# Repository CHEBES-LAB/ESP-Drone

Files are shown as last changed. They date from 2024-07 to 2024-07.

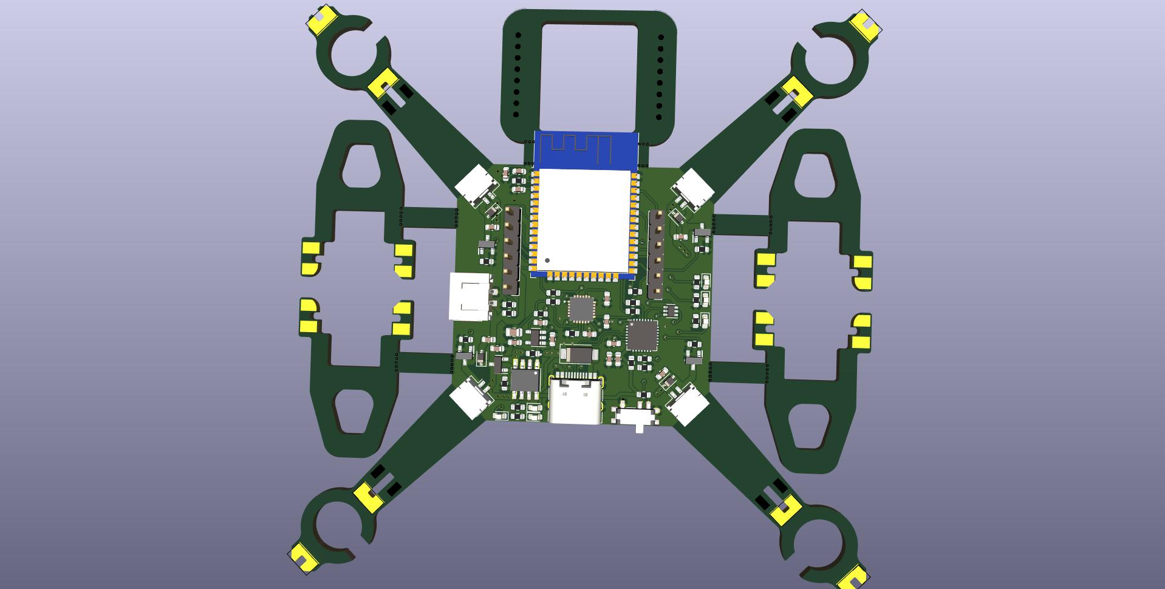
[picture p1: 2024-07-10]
Hardware/PDF/ESP32 drone.jpg

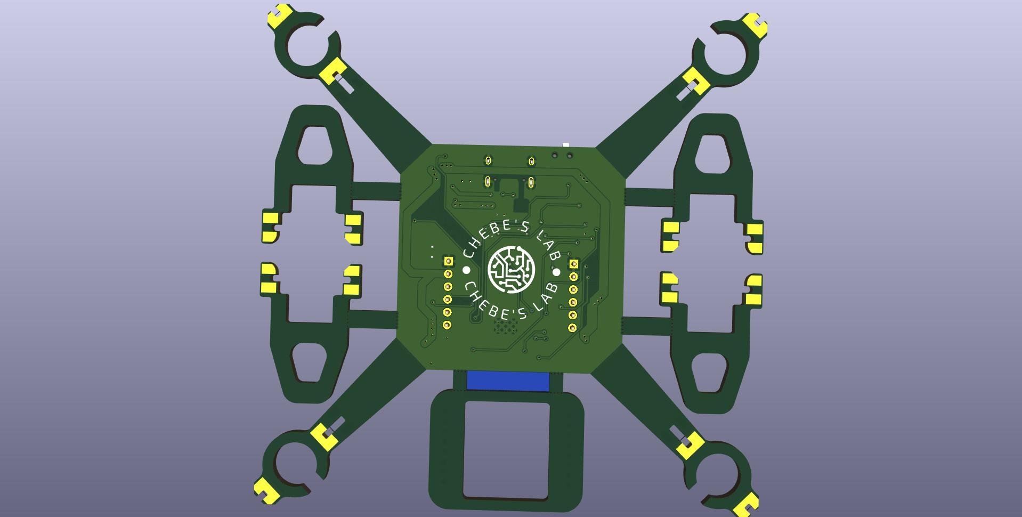
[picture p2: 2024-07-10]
Hardware/PDF/ESP32 drone back.jpg

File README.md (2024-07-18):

# ESP-Drone

image_tooltip

<br>

<br>

For a full tutorial check out our [ESP32 Drone Article](https://circuitdigest.com/microcontroller-projects/DIY-wifi-controlled-drone).
For working video:  [How to build an ESP32 Drone](https://youtu.be/uzZjk0TQKtU).

Drones have rapidly evolved from niche hobbies to versatile tools with a wide range of applications, from photography to agriculture or even for defense and military purposes. Depending on the application, features and payload capacity their price will vary from pocket changes to a few million. Even though the basic principle behind these drones may appear simple, there is a lot of technology and computation that goes behind it for proper operations and a desired result from these drones. For example, maintaining stability while in the air requires precision sensors such as a Gyroscope and proper processing of reading taken with it. In this project we are going to make such a drone which can be easily controlled using our phones.
This DIY drone is small in size and can be built using easily available components such as ESP32 modules, MPU6050 IMU, coreless motors and plastic propellers.
<br>For anyone who is trying to flash the firmware using ESP32 Flash Download Tool, here are the file offsets for each binary
<br>0x1000 bootloader.bin
<br>0x10000 ESPDrone.bin
<br>0x8000 partition-table.bin
<br>
[Note: As this projects are very simple we are only providing the code, schemaitic, and a few essential images if you want to get the images or code explanations do check out the Circuit Digest website.
<br>
<br>

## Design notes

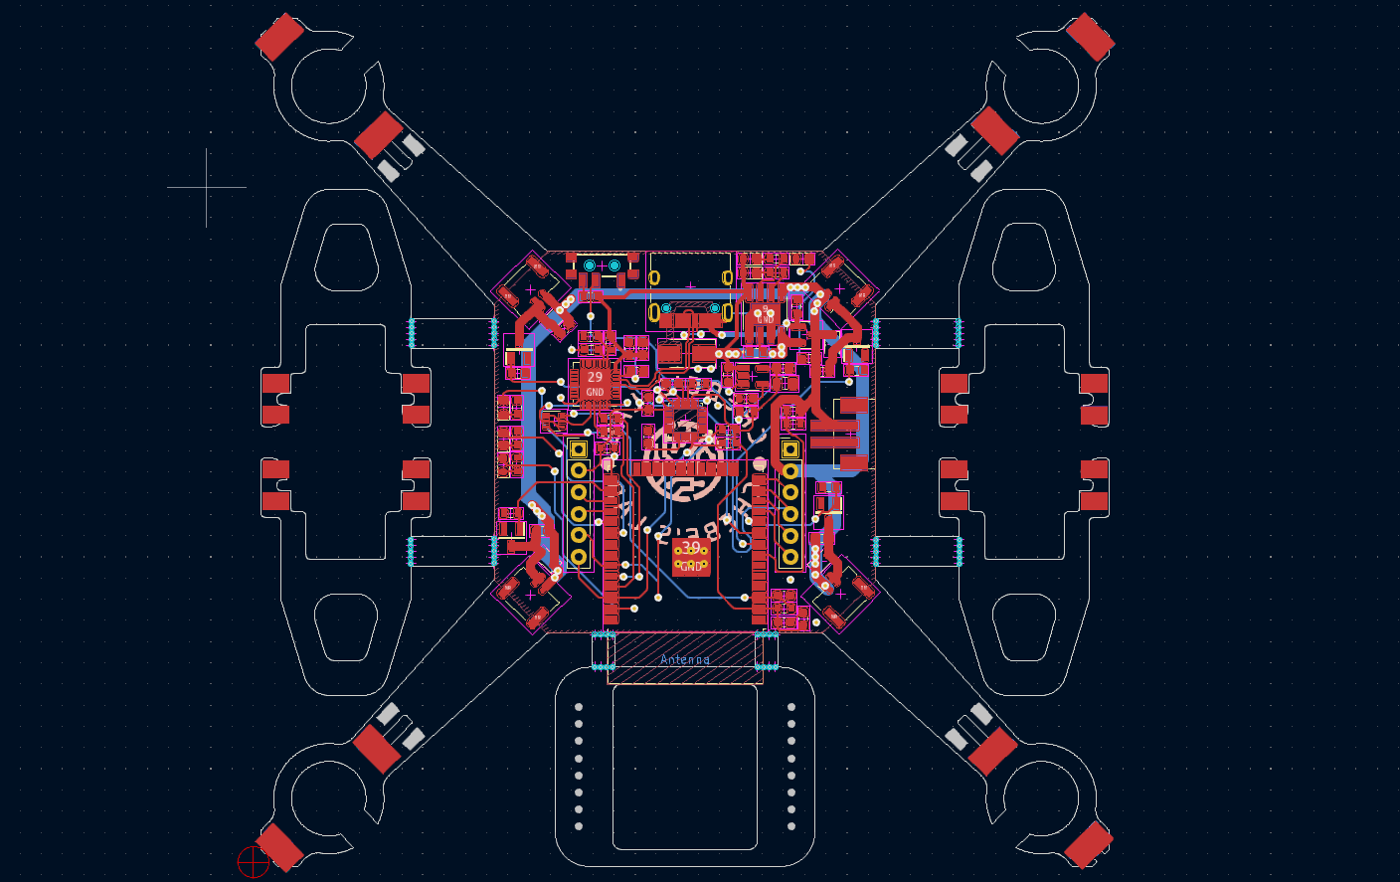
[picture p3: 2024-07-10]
Hardware/PDF/PCB .png

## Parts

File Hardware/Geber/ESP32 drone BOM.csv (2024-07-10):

Reference | Value | Datasheet | Footprint | Qty | DNP
C1,C4 | 10u | ~ | Capacitor_SMD:C_0603_1608Metric | 2
C2 | 470pF | ~ | Capacitor_SMD:C_0603_1608Metric | 1
C3 | 2.2uF | ~ | Capacitor_SMD:C_0805_2012Metric | 1
C5 | 10uF | ~ | Capacitor_SMD:C_0603_1608Metric | 1
C6,C11,C12,C13 | 0.1uf | ~ | Capacitor_SMD:C_0603_1608Metric | 4
C7,C9,C14 | 10uf | ~ | Capacitor_SMD:C_0603_1608Metric | 3
C8,C10,C15,C16,C17,C18 | 1uf | ~ | Capacitor_SMD:C_0603_1608Metric | 6
D1 | SS34 | https://www.diodes.com/assets/Datasheets/ds16008.pdf | Diode_SMD:D_SMA | 1
D2,D3,D4,D5 | 1N4148W | https://www.vishay.com/docs/85748/1n4148w.pdf | Diode_SMD:D_SOD-323 | 4
IC1 | TP4056 |  | AddedLibraries:SOP127P600X175-9N | 1
J1 | USB_C_Receptacle_USB2.0 | https://www.usb.org/sites/default/files/documents/usb_type-c.zip | Connector_USB:USB_C_Receptacle_HRO_TYPE-C-31-M-12 | 1
J2,J4,J5,J6 | Conn_01x02_Female | ~ | Connector_JST:JST_GH_SM02B-GHS-TB_1x02-1MP_P1.25mm_Horizontal | 4
J3 | B2B-PH-SM4-TB_LF__SN_ |  | AddedLibraries:SM4-CON | 1
J8,J9 | Conn_01x06_Female | ~ | Connector_PinHeader_2.54mm:PinHeader_1x06_P2.54mm_Vertical | 2
LED1 | POW_LED | ~ | LED_SMD:LED_0603_1608Metric | 1
LED2,LED3 | CHG | ~ | LED_SMD:LED_0603_1608Metric | 2
LED4,LED5,LED6 | LED | ~ | LED_SMD:LED_0603_1608Metric | 3
R1 | 470R | ~ | Resistor_SMD:R_0603_1608Metric | 1
R2,U1,U4,U5 | 100K | ~ | Resistor_SMD:R_0603_1608Metric | 4
R3,R4 | 1.3K | ~ | Resistor_SMD:R_0603_1608Metric | 2
R5 | 47.5k | ~ | Resistor_SMD:R_0603_1608Metric | 1
R6 | 22.1k | ~ | Resistor_SMD:R_0603_1608Metric | 1
R7,R10,R11,R12,R14,R18,R19,R20,R21 | 10k | ~ | Resistor_SMD:R_0603_1608Metric | 9
R8,R9 | 1k | ~ | Resistor_SMD:R_0603_1608Metric | 2
R13 | 4.7k | ~ | Resistor_SMD:R_0603_1608Metric | 1
R15,R16,R17 | 1K | ~ | Resistor_SMD:R_0603_1608Metric | 3
Rprog1 | 3.3K | ~ | Resistor_SMD:R_0603_1608Metric | 1
SW1 | CUS-12TB |  | AddedLibraries:CUS-12B | 1
T1,T2,T3,T4 | SI2302DS-T1 | https://4donline.ihs.com/images/VipMasterIC/IC/SILX/SILXS08192/SILXS08192-1.pdf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 | AddedLibraries:SOT95P237X112-3N | 4
U2 | AO3401 | ~ | Package_TO_SOT_SMD:SOT-23 | 1
U3 | MIC5219-3.3YM5 | http://ww1.microchip.com/downloads/en/DeviceDoc/MIC5219-500mA-Peak-Output-LDO-Regulator-DS20006021A.pdf | Package_TO_SOT_SMD:SOT-23-5 | 1
U6 | CP2102N-Axx-xQFN28 | https://www.silabs.com/documents/public/data-sheets/cp2102n-datasheet.pdf | Package_DFN_QFN:QFN-28-1EP_5x5mm_P0.5mm_EP3.35x3.35mm | 1
U7 | DDC114TU-7-F |  | Package_TO_SOT_SMD:SOT-363_SC-70-6 | 1
U8 | ESP32-WROOM-32 | https://www.espressif.com/sites/default/files/documentation/esp32-wroom-32_datasheet_en.pdf | RF_Module:ESP32-WROOM-32 | 1
U9 | MPU-6050 |  | AddedLibraries:QFN50P400X400X95-24N | 1

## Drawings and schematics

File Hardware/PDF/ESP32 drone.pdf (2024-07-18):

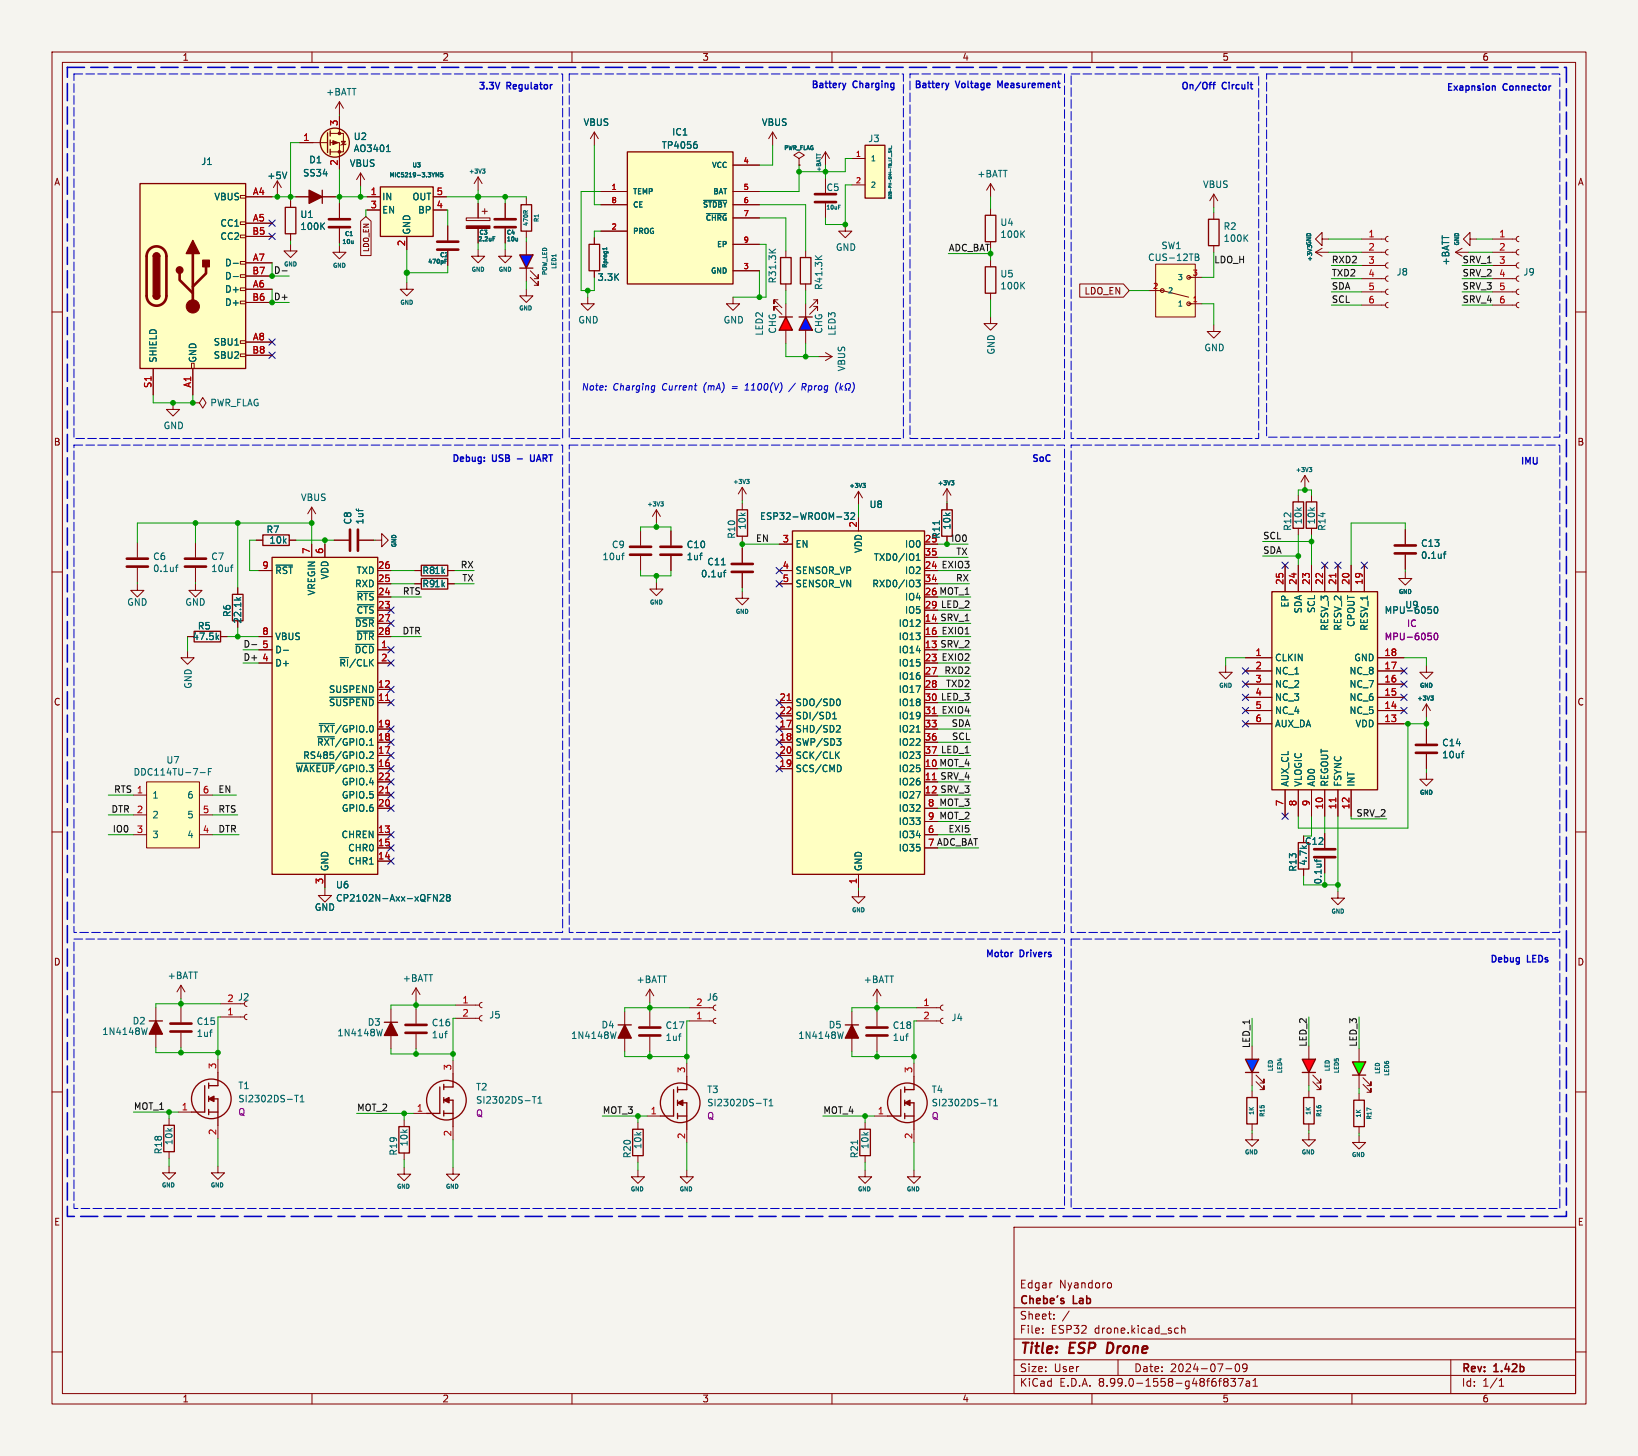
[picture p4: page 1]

Battery Voltage Measurement SoC

9 RESV_3 22 REGOUT 10 RESV_2 21 FSYNC 11 CPOUT 20 INT 12 RESV_1 19 GND 18 NC_8 17 NC_7 16 NC_6 15 NC_5 14 VDD 13 C12 0.1uf R134.7k U8 ESP32-WROOM-32 EN 3 SENSOR_VP 4 SENSOR_VN 5 SDO/SD0 21 SDI/SD1 22 SHD/SD2 17 SWP/SD3 18 SCK/CLK 20 SCS/CMD 19 VDD

3 TXD 26 RXD 25 ~{RTS} 24 ~{CTS} 23 ~{DSR} 27 ~{DTR} 28 ~{DCD}1 ~{RI}/CLK2 SUSPEND 12 ~{SUSPEND}11 ~{TXT}/GPIO.019 ~{RXT}/GPIO.118 RS485/GPIO.2 17 ~{WAKEUP}/GPIO.316 GPIO.4 22 GPIO.5 21 GPIO.6 20 CHREN 13 CHR0 15 CHR1 14 R7
4 U7 DDC114TU-7-F GND

3 TXD 26 RXD 25 ~{RTS} 24 ~{CTS} 23 ~{DSR} 27 ~{DTR} 28 ~{DCD}1 ~{RI}/CLK2 SUSPEND 12 ~{SUSPEND}11 ~{TXT}/GPIO.019 ~{RXT}/GPIO.118 RS485/GPIO.2 17 ~{WAKEUP}/GPIO.316 GPIO.4 22 GPIO.5 21 GPIO.6 20 CHREN 13 CHR0 15 CHR1 14 U6 CP2102N-Axx-xQFN28 GND

9 RESV_3 22 REGOUT 10 RESV_2 21 FSYNC 11 CPOUT 20 INT 12 RESV_1 19 GND 18 NC_8 17 NC_7 16 NC_6 15 NC_5 14 VDD 13 U9 MPU-6050

Id: 1/1 Title: ESP Drone

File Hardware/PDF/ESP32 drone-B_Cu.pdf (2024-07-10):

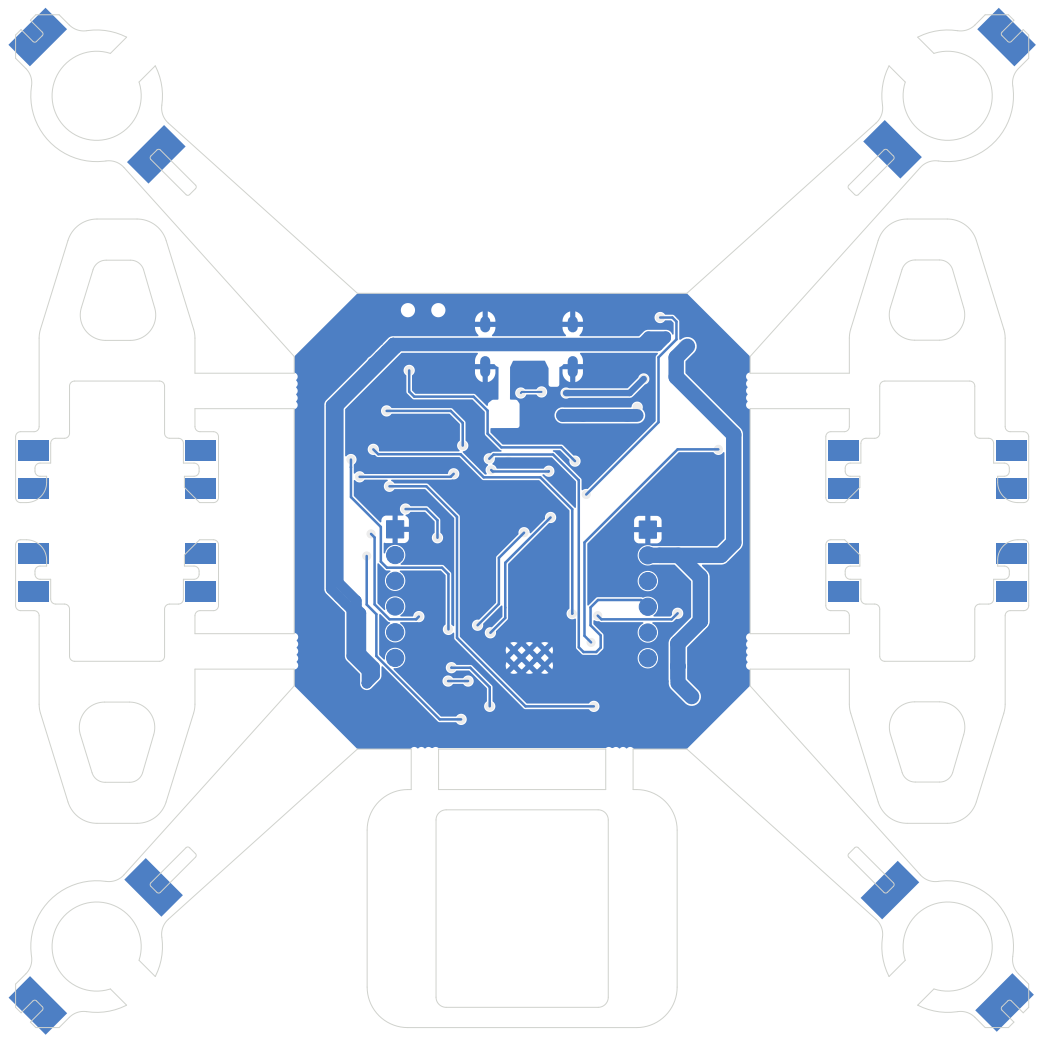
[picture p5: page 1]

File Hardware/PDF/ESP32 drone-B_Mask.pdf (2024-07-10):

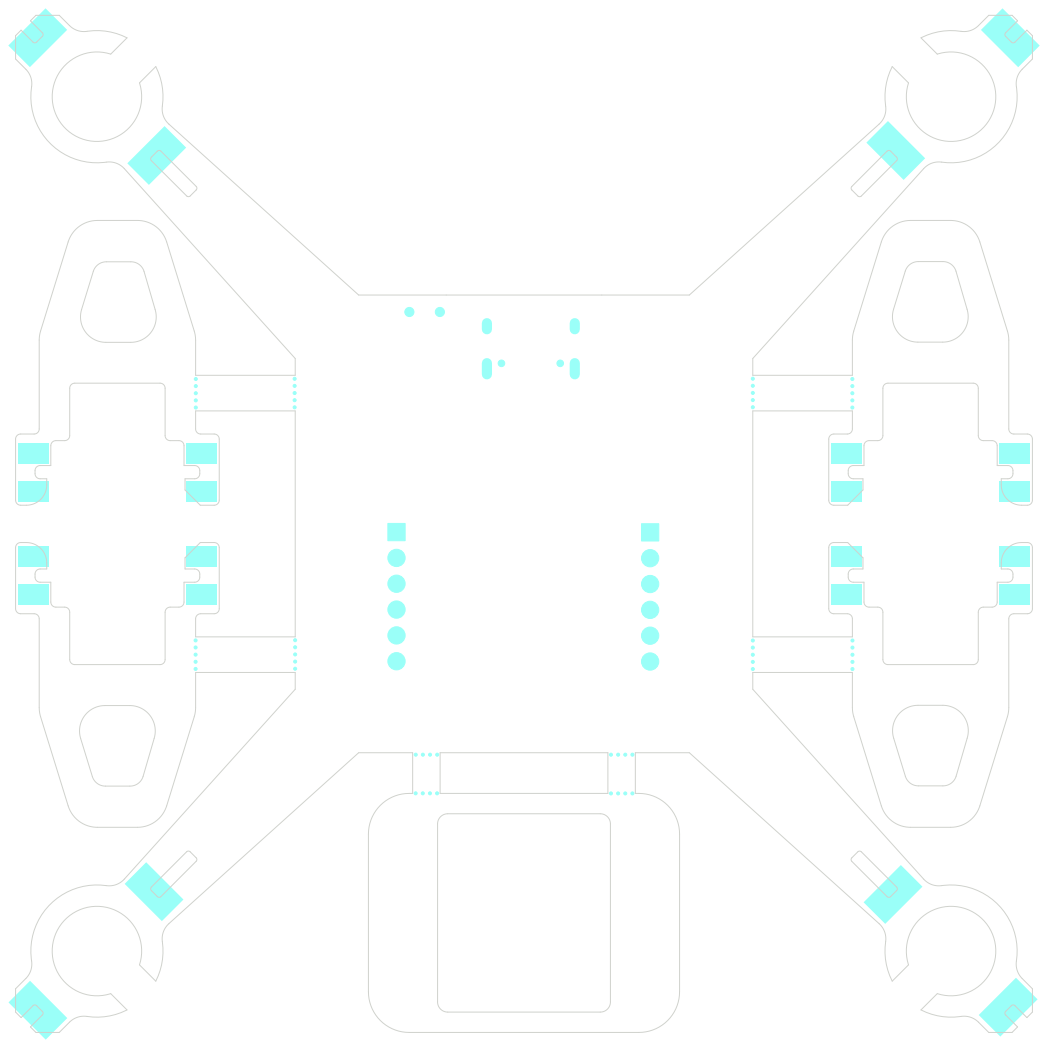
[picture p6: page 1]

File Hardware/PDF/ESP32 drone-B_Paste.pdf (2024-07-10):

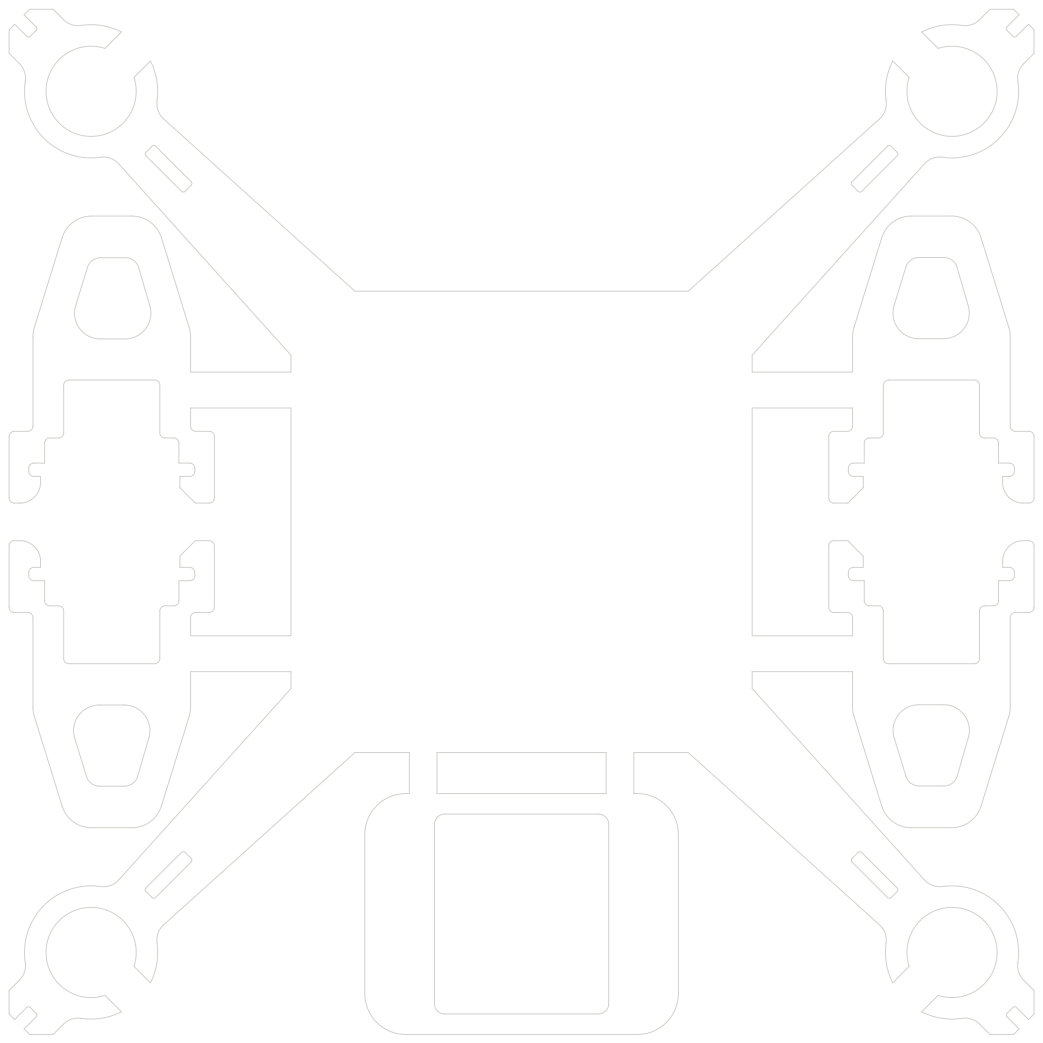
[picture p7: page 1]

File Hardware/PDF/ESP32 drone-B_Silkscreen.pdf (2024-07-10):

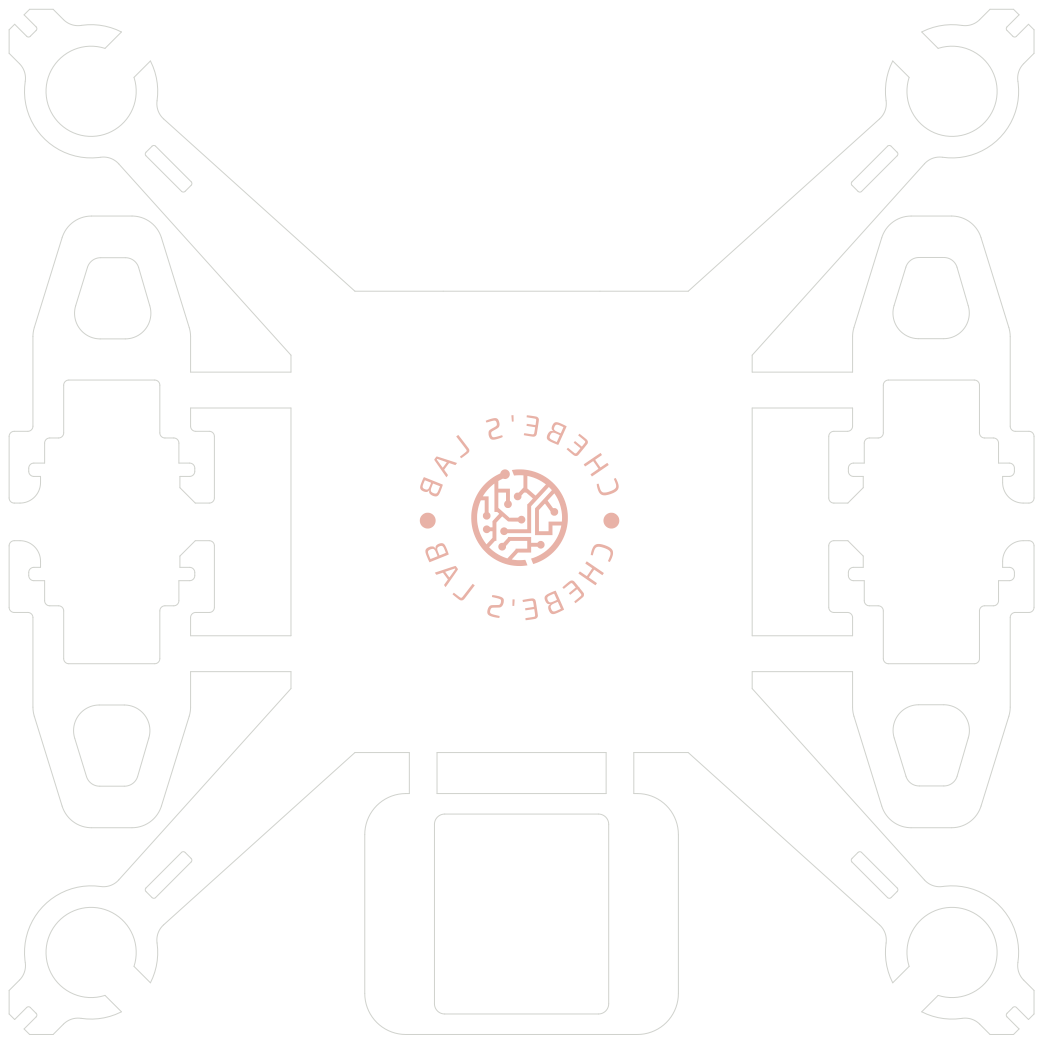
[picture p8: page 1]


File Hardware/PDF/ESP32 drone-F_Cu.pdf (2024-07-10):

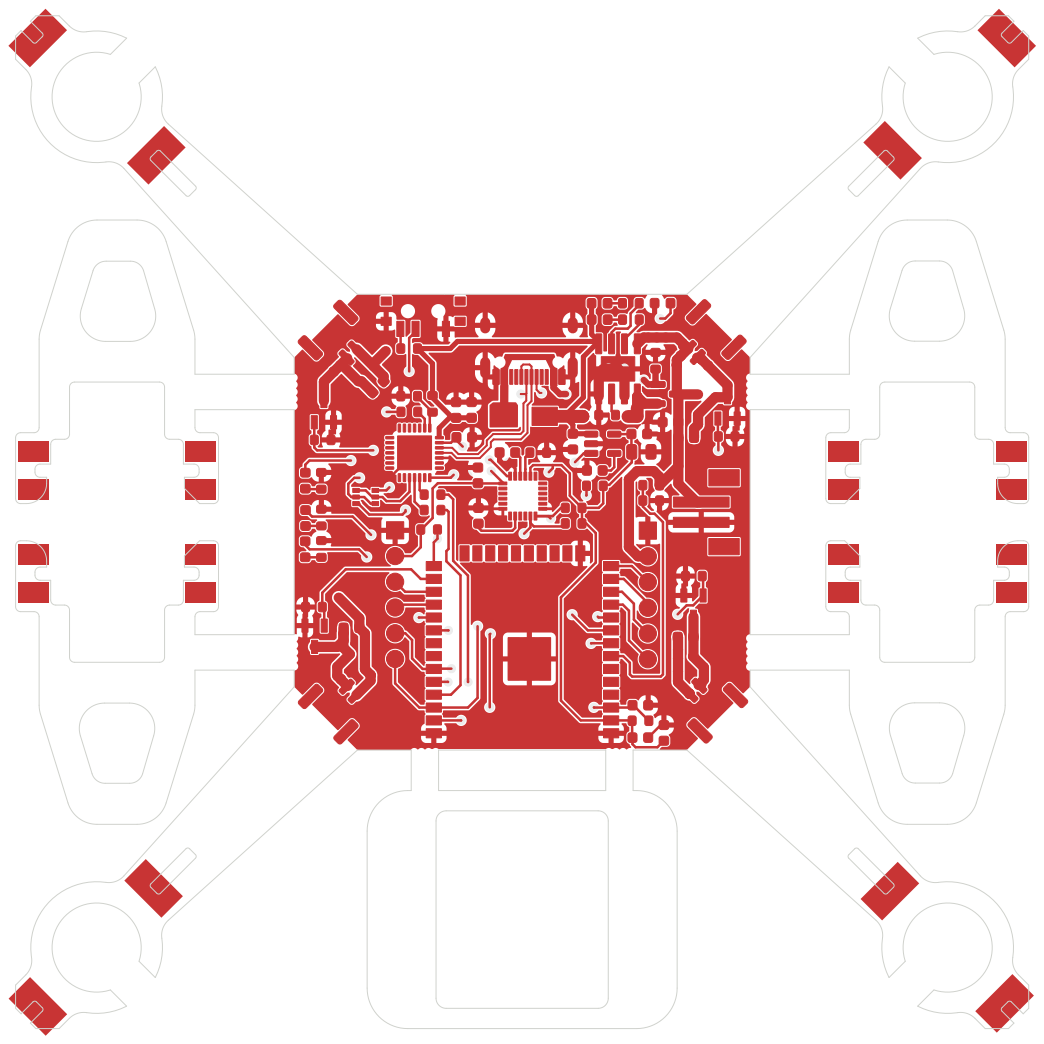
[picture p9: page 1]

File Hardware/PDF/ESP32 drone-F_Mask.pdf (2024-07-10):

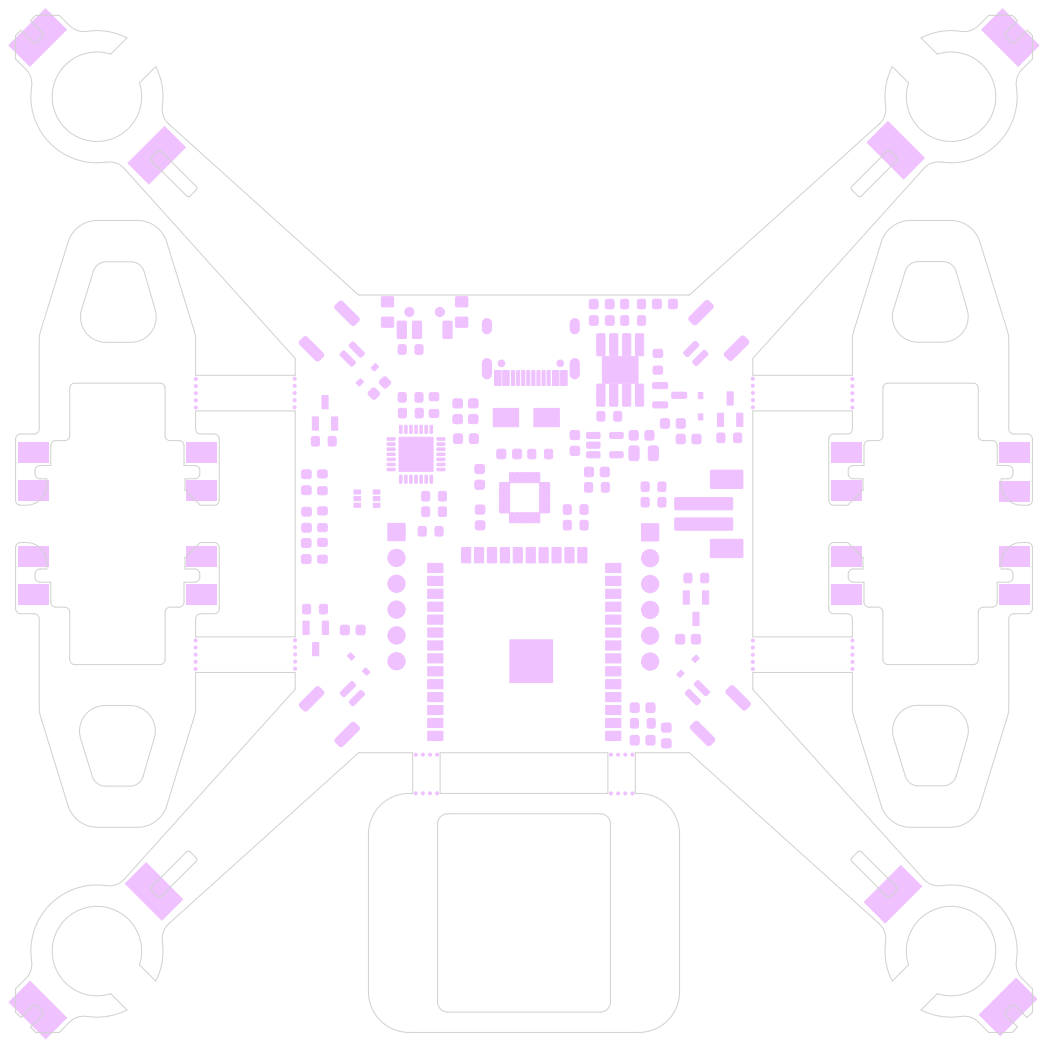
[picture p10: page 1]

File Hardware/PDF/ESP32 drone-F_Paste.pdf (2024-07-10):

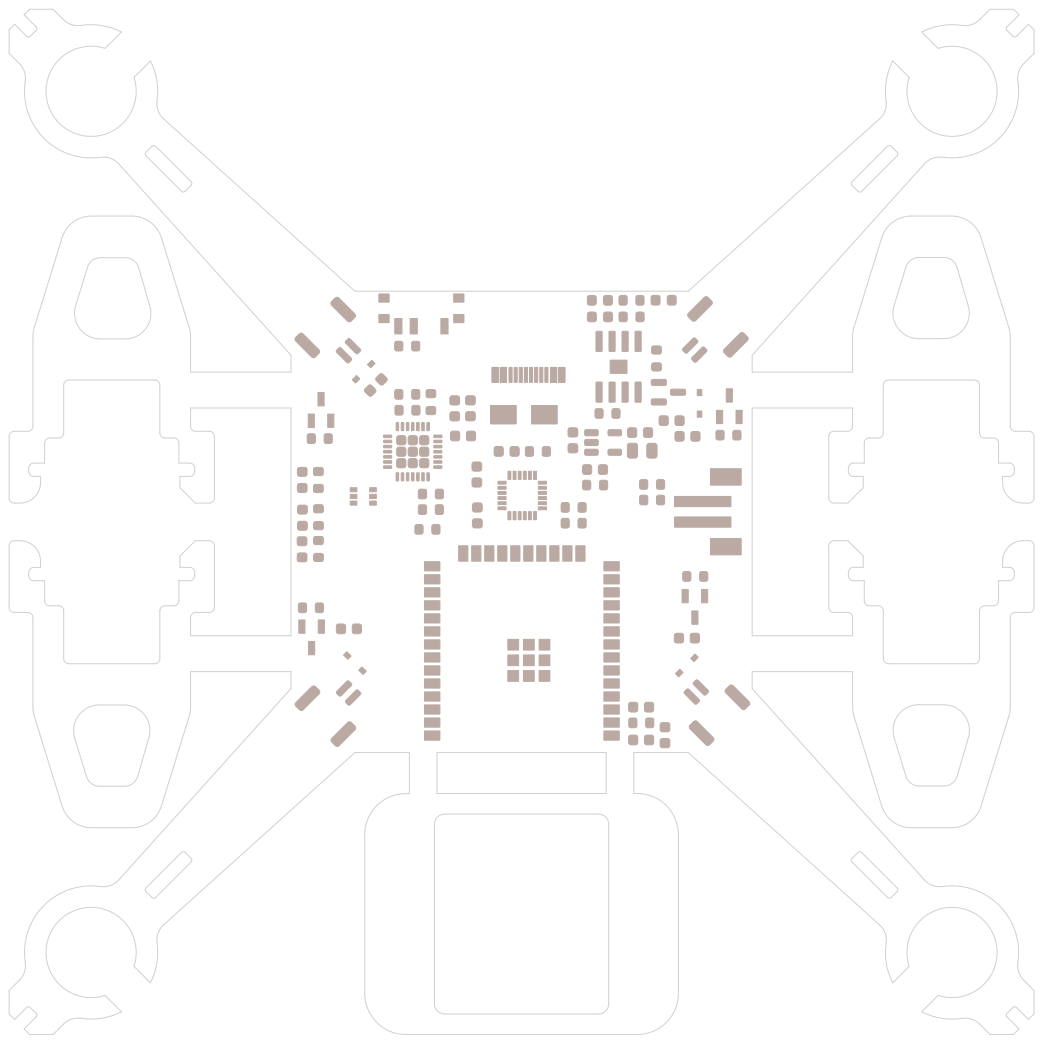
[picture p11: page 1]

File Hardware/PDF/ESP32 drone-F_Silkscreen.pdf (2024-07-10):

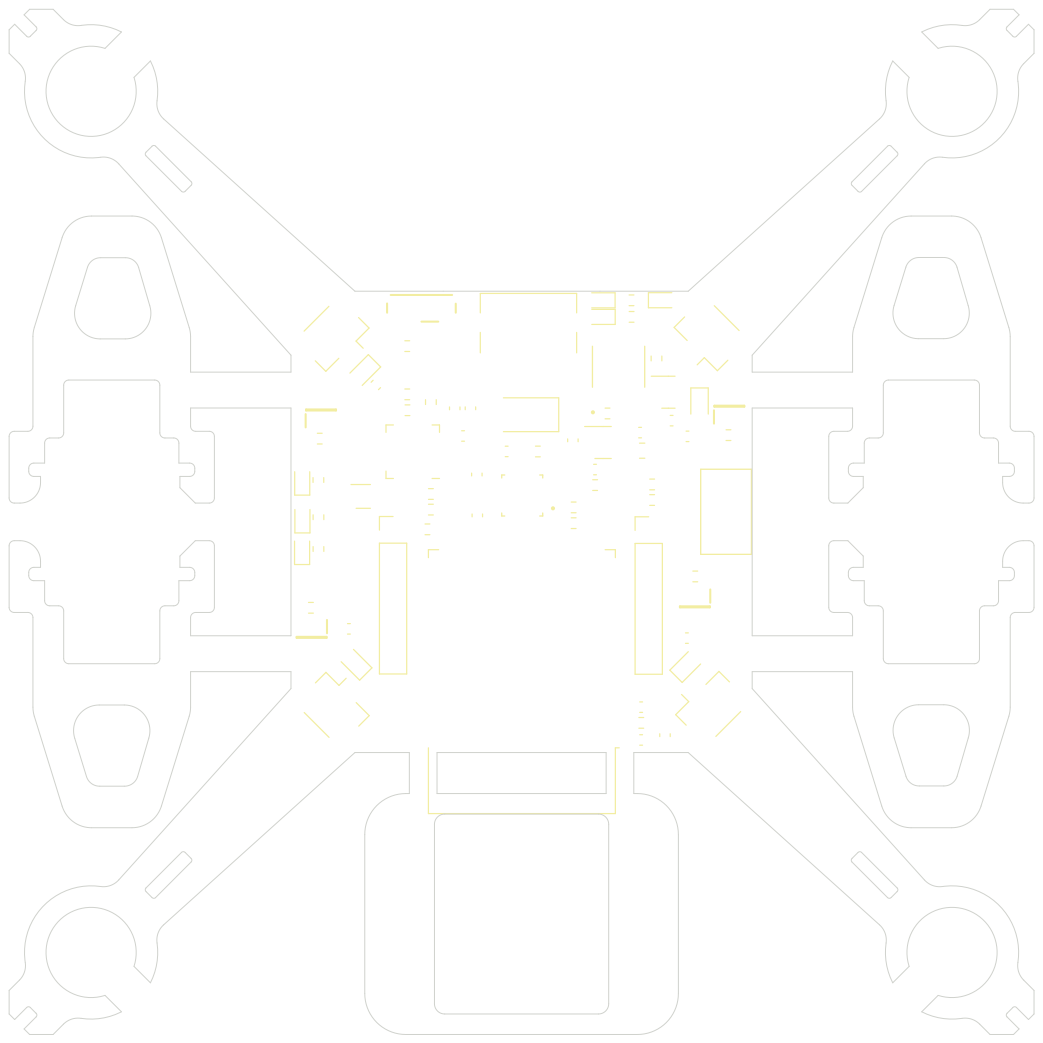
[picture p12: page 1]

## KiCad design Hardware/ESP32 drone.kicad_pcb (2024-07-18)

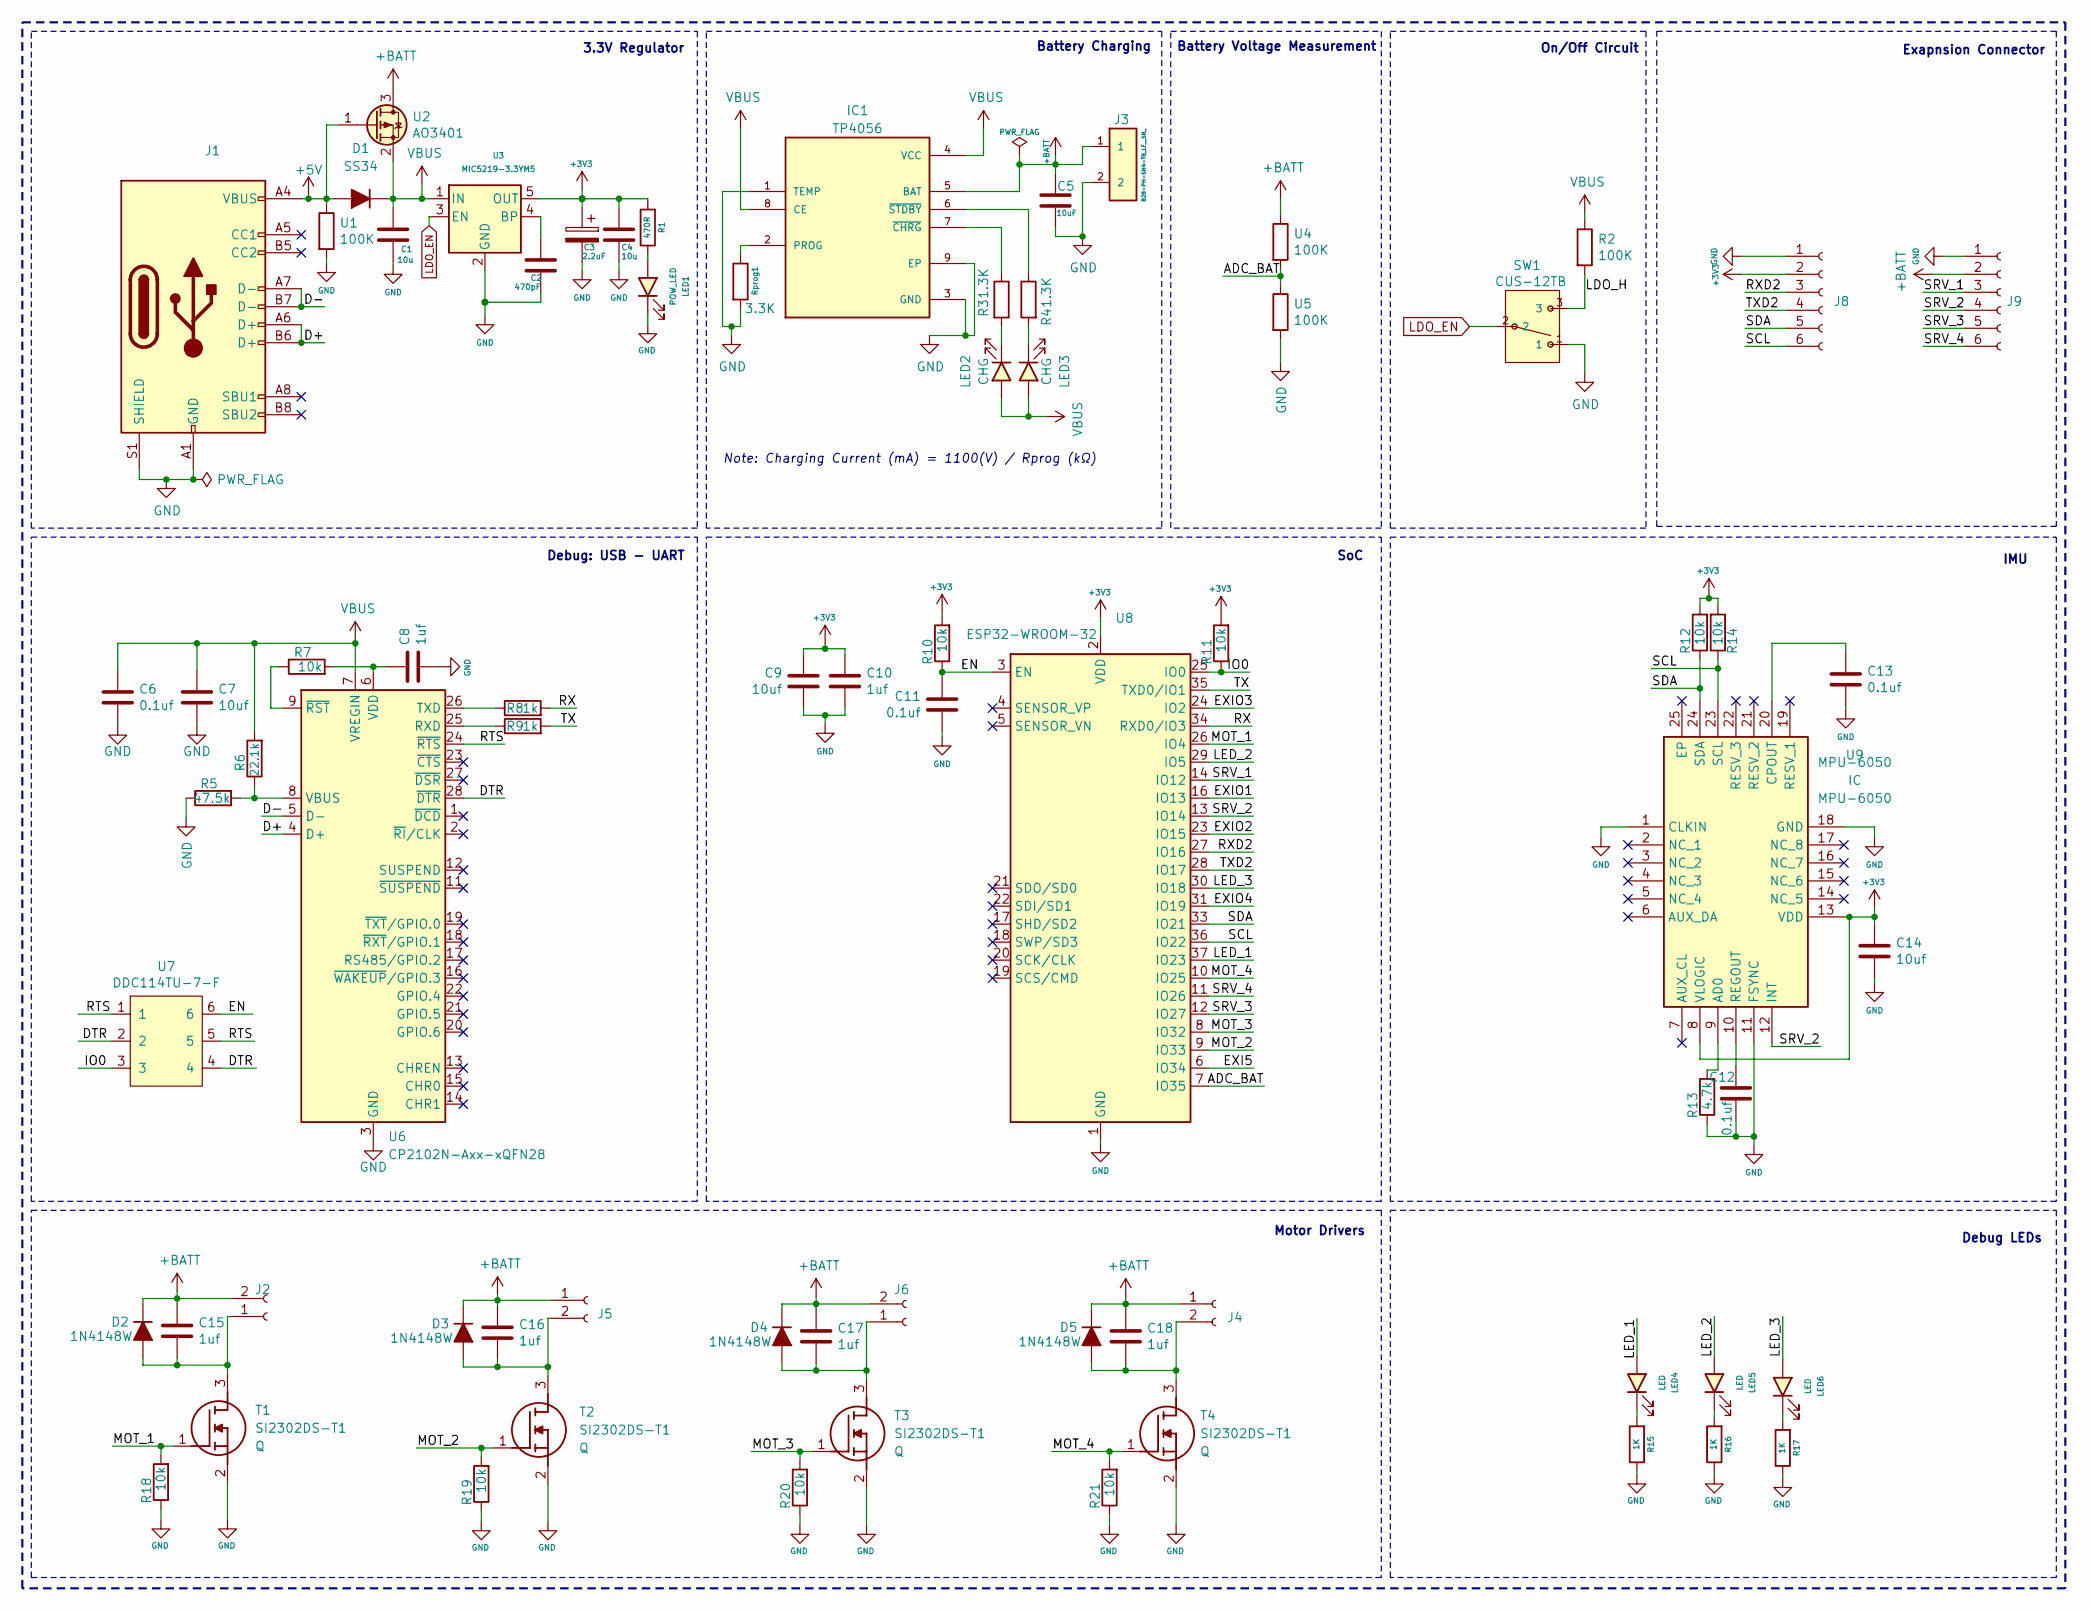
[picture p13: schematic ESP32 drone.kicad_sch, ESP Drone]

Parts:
C1, C4: 10u; C_0603_1608Metric
C2: 470pF; C_0603_1608Metric
C3: 2.2uF; C_0805_2012Metric
C5: 10uF; C_0603_1608Metric
C6, C11, C12, C13: 0.1uf; C_0603_1608Metric
C7, C9, C14: 10uf; C_0603_1608Metric
C8, C10, C15, C16, C17, C18: 1uf; C_0603_1608Metric
D1: SS34; D_SMA
D2, D3, D4, D5: 1N4148W; D_SOD-323
IC1: TP4056; SOP127P600X175-9N
J1: USB_C_Receptacle_USB2.0; USB_C_Receptacle_HRO_TYPE-C-31-M-12
J2, J4, J5, J6: Conn_01x02_Female; JST_GH_SM02B-GHS-TB_1x02-1MP_P1.25mm_Horizontal
J3: B2B-PH-SM4-TB_LF__SN_; SM4-CON
J8, J9: Conn_01x06_Female; PinHeader_1x06_P2.54mm_Vertical
LED1: POW_LED; LED_0603_1608Metric
LED2, LED3: CHG; LED_0603_1608Metric
LED4, LED5, LED6: LED; LED_0603_1608Metric
R1: 470R; R_0603_1608Metric
R2: 100K; R_0603_1608Metric
R3, R4: 1.3K; R_0603_1608Metric
R5: 47.5k; R_0603_1608Metric
R6: 22.1k; R_0603_1608Metric
R7, R10, R11, R12, R14, R18, R19, R20, R21: 10k; R_0603_1608Metric
R8, R9: 1k; R_0603_1608Metric
R13: 4.7k; R_0603_1608Metric
R15, R16, R17: 1K; R_0603_1608Metric
Rprog1: 3.3K; R_0603_1608Metric
SW1: CUS-12TB; CUS-12B; MANUFACTURER_PART_NUMBER CUS-12TB
T1, T2, T3, T4: SI2302DS-T1; SOT95P237X112-3N; Mouser Part Number 781-SI2302DS
U1, U4, U5: 100K; R_0603_1608Metric
U2: AO3401; SOT-23
U3: MIC5219-3.3YM5; SOT-23-5
U6: CP2102N-Axx-xQFN28; QFN-28-1EP_5x5mm_P0.5mm_EP3.35x3.35mm
U7: DDC114TU-7-F; SOT-363_SC-70-6
U8: ESP32-WROOM-32
U9: MPU-6050; QFN50P400X400X95-24N; Mouser Part Number 410-MPU-6050

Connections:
+3V3: C3.1, C4.1, C9.1, C10.1, C14.1, J8.2, R1.2, R10.2, R11.2, R12.2, R14.2, U3.5 (OUT), U8.2 (VDD), U9.8 (VLOGIC), U9.13 (VDD)
+5V: D1.2 (A), J1.A4 (VBUS), J1.A9 (VBUS), J1.B4 (VBUS), J1.B9 (VBUS), U1.1, U2.1 (G)
+BATT: C5.1, C15.1, C16.1, C17.1, C18.1, D2.1 (K), D3.1 (K), D4.1 (K), D5.1 (K), IC1.5 (BAT), J2.2, J3.1, J4.1, J5.1, J6.2, J9.2, U2.3 (D), U4.1
/ADC_BAT: U4.2, U5.1, U8.7 (IO35)
/D+: J1.A6 (D+), J1.B6 (D+), U6.4 (D+)
/D-: J1.A7 (D-), J1.B7 (D-), U6.5 (D-)
/DTR: U6.28 (~DTR), U7.2, U7.4
/EN: C11.1, R10.1, U7.6, U8.3 (EN)
/EXI5: U8.6 (IO34)
/EXIO1: U8.16 (IO13)
/EXIO2: U8.23 (IO15)
/EXIO3: U8.24 (IO2)
/EXIO4: U8.31 (IO19)
/IO0: R11.1, U7.3, U8.25 (IO0)
/LDO_H: R2.2, SW1.3 (C)
/LED_1: LED4.2 (A), U8.37 (IO23)
/LED_2: LED5.2 (A), U8.29 (IO5)
/LED_3: LED6.2 (A), U8.30 (IO18)
/MOT_1: R18.2, T1.1 (G), U8.26 (IO4)
/MOT_2: R19.2, T2.1 (G), U8.9 (IO33)
/MOT_3: R20.2, T3.1 (G), U8.8 (IO32)
/MOT_4: R21.2, T4.1 (G), U8.10 (IO25)
/RTS: U6.24 (~RTS), U7.1, U7.5
/RX: R8.2, U8.34 (RXD0/IO3)
/RXD2: J8.3, U8.27 (IO16)
/SCL: J8.6, R14.1, U8.36 (IO22), U9.23 (SCL)
/SDA: J8.5, R12.1, U8.33 (IO21), U9.24 (SDA)
/SRV_1: J9.3, U8.14 (IO12)
/SRV_2: J9.4, U8.13 (IO14), U9.12 (INT)
/SRV_3: J9.5, U8.12 (IO27)
/SRV_4: J9.6, U8.11 (IO26)
/TX: R9.2, U8.35 (TXD0/IO1)
/TXD2: J8.4, U8.28 (IO17)
GND: C1.2, C2.2, C3.2, C4.2, C5.2, C6.2, C7.2, C8.2, C9.2, C10.2, C11.2, C12.2, C13.2, C14.2, IC1.1 (TEMP), IC1.3 (GND), IC1.9 (EP), J1.A1 (GND), J1.A12 (GND), J1.B1 (GND), J1.B12 (GND), J1.S1 (SHIELD), J3.2, J8.1, J9.1, LED1.1 (K), R5.1, R13.1, R15.1, R16.1, R17.1, R18.1, R19.1, R20.1, R21.1, Rprog1.2, SW1.1 (A), SW1.4, T1.2 (S), T2.2 (S), T3.2 (S), T4.2 (S), U1.2, U3.2 (GND), U5.2, U6.3 (GND), U6.29 (GND), U8.1 (GND), U8.15 (GND), U8.38 (GND), U8.39 (GND), U9.1 (CLKIN), U9.11 (FSYNC), U9.18 (GND)
LDO_EN: SW1.2 (B), U3.3 (EN)
unnamed: C15.2, D2.2 (A), J2.1, T1.3 (D)
unnamed: C16.2, D3.2 (A), J5.2, T2.3 (D)
unnamed: C17.2, D4.2 (A), J6.1, T3.3 (D)
unnamed: C18.2, D5.2 (A), J4.2, T4.3 (D)
unnamed: IC1.2 (PROG), Rprog1.1
unnamed: IC1.7 (~CHRG), R3.1
unnamed: IC1.6 (~STDBY), R4.1
unnamed: LED1.2 (A), R1.1
unnamed: LED2.1 (K), R3.2
unnamed: LED3.1 (K), R4.2
unnamed: LED4.1 (K), R15.2
unnamed: LED5.1 (K), R16.2
unnamed: LED6.1 (K), R17.2
unnamed: C2.1, U3.4 (BP)
unnamed: R9.1, U6.25 (RXD)
unnamed: R8.1, U6.26 (TXD)
unnamed: R5.2, R6.1, U6.8 (VBUS)
unnamed: C8.1, R7.2, U6.6 (VDD)
unnamed: R7.1, U6.9 (~RST)
unnamed: R13.2, U9.9 (AD0)
unnamed: C13.1, U9.20 (CPOUT)
unnamed: C12.1, U9.10 (REGOUT)
VBUS: C1.1, C6.1, C7.1, D1.1 (K), IC1.4 (VCC), IC1.8 (CE), LED2.2 (A), LED3.2 (A), R2.1, R6.2, U2.2 (S), U3.1 (IN), U6.7 (VREGIN)

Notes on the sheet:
SoC
Battery Voltage Measurement
IMU
Motor Drivers
Battery Charging
Debug LEDs
Debug: USB - UART
Exapnsion Connector
3.3V Regulator
Note: Charging Current (mA) = 1100(V) / Rprog (kΩ)
On/Off Circuit

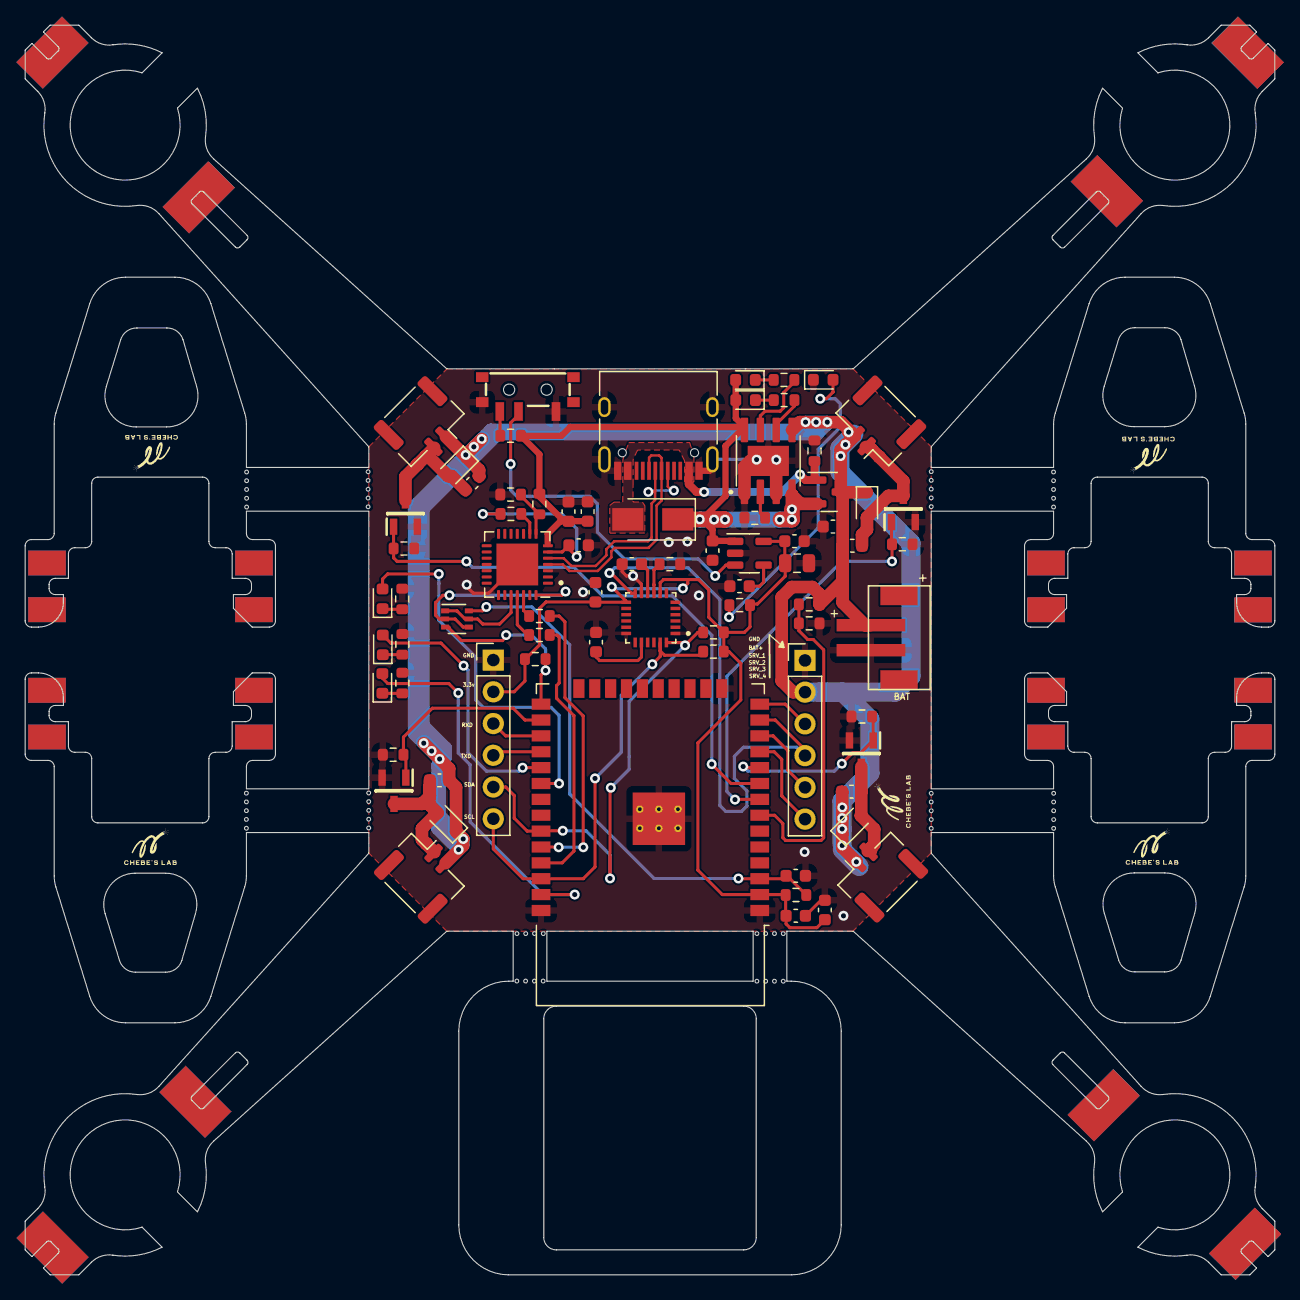
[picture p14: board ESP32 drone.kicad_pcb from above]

Board: 2 copper layers, 100.0 x 100.0 mm, 74 parts (0 on the bottom side), 53 nets.
